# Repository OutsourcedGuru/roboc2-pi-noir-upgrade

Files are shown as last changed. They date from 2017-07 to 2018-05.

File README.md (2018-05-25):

# roboc2-pi-noir-upgrade
Step-by-step instructions for adding a Pi NoIR webcam to the Robo C2 printer.

## Order Parts
For this project, you'll need three mandatory parts and one that's optional. The mandatory parts are the [Raspberry Pi NoIR Camera Board v2 - 8 Megapixels](https://www.adafruit.com/product/3100) ($26.99), a longer [Flex Cable for Raspberry Pi - 18"](https://www.adafruit.com/product/1730) ($2.50) given the distance and lastly, a [medium-sized suction cup](http://www.peakbanner.com/banner-clear-suction-cup-hook-set-4pcs?gclid=CKq-oPKxvtQCFY6cfgodSF4LQQ) ($0.99) from Ace Hardware, for example. I personally purchased my webcam from Fry's Electronics and the ribbon cable from Adafruit.com online.

As for the optional part, I chose to upgrade the microSD on the Robo C2's internal Raspberry Pi 3 from 4GB to 16GB given that the resolution on the new v2 webcam is 8MP (which could be as much as 1GB storage per 8 minutes of video). I chose the [SanDisk Ultra PLUS microSDHC UHS-1 Card with Adapter](http://www.frys.com/product/8654990?site=sr:SEARCH:MAIN_RSLT_PG) from Fry's Electronics ($9.99) for this. The total cost for the full upgrade is about $41 plus tax/shipping, as appropriate, plus any incremental cost to print the enclosure.

Additionally, if your workstation does not have an SD or a microSD slot, you will need some sort of external USB adapter for cloning the microSD card.

## Software
Since we'll be saving an image of the existing microSD and restoring that to the new card, I downloaded and installed [ApplePi-Baker for OS X](https://www.tweaking4all.com/software/macosx-software/macosx-apple-pi-baker/). If you're on Windows for your workstation then you'll need some software to clone microSD cards.

## 3D Part
For this project, you'll need to print the enclosure in PLA. I used the [Robo White PLA](https://store.robo3d.com/collections/filament-pla/products/white-pla-1-kg-spool) for this but any standard PLA filament should work for this.

pi-noir-part

I've created some custom filament profiles for Cura and have stored them in [this repository](https://github.com/OutsourcedGuru/cura-filament-profiles) should you need some. Since it's assumed that you have a Robo C2, I've included the GCODE file which should be ready to print. As a result, you shouldn't even need to go into Cura for this.

## Instructions
Verify that you have all the parts you'll need to begin and a few tools to include a pair of pliers.

required-parts

I purchased two ribbon cables of different lengths (12" and 18") to do some test fitting. If you don't mind the cable being seen inside the black enclosure of the Robo C2 then the 12" will be fine; otherwise, go with the 18" cable as I've done.

It's necessary to do some slight cleanup of the inside of the Pi NoIR printed part but some of the remainder of the support actually is useful to hold the camera in. I didn't find it necessary to use any glue to hold the enclosure together but you'll want to do a test fit later to verify.

### Power on your Robo C2 to raise the bed
Once it has booted, ignore any prompts to upgrade the software at this time by choosing Cancel.

**Motor Control** -> using **Z=100mm** setting, press the **Z-** option once *and only once*! Adjust to the **Z=1mm** setting and continue raising it with **Z-** (but not so high that the bed hits the extruder).

motor-controls

### Save your z-offset
In the LCD menu, select Utilities -> Options -> EEPROM -> Home Offsets and write down your current setting here for Z.

z-offset

It's possible after upgrading your software that this value may be set back to the default. Given that this is a fussy adjustment, it's good to have this information available.

### Power off your Robo C2
Use the power switch in the back to abrubtly power off the printer (without it homing the steppers).

### Remove the base and front covers
Use the latch in the front to remove the base cover. Reach inside to pop loose the front cover at the top. Work around to the latches on the sides and then ease off the front panel. Leave the connections in place.

front-1
front-2
front-3

It's good to have a strong light so that you can see things inside.

### Pull the microSD card
Find the Raspberry Pi 3 computer on the left and locate its microSD card which is just sticking out from the bottom of the board. Slide this out with your fingers.

microsd-location

Using the SD adapter which comes with the new microSD card, insert the existing 4GB microSD card from the Robo C2 into this SD adapter and then into your workstation.

microsd-original

If your workstation does not have an SD adapter slot, you might need a USB adapter which accommodates a microSD card.

### Begin backup of your image
It's probably a good idea to verify that your workstation has at least 4GB of free space. If not, you'll need to clear some up to make this image. In OS X, you right-mouse click the hard drive in Finder and choose Get Info.

available-space

I use ApplePi-Baker for this step. Select the 4GB microSD card from the Robo C2 and choose the Create Backup option. Give your image a useful name and select ZIP as the Format option. Choose Save and while this is backing up, continue with the physical installation of the camera.

backup-1
[backup-2](https://user-images.githubusercontent.com/15971213/27871419-76214bb4-615a-11e7-9f85-c6eaef0330d9.png)

### Replace the ribbon cable on your camera
Unbox the Pi NoIR camera. Push the black clip near the ribbon cable so that it's moved away from the board by a couple of millimeters. Then remove the existing ribbon cable, noting the direction of the silver connectors at the end.

ribbon-1
ribbon-2

Insert one end of the new 18" replacement ribbon cable, making sure that the silver connectors face the same way as before. Push the black clip back down into place so that it will hold the ribbon cable snugly.

ribbon-3
ribbon-4
ribbon-5

Remove the small protective film from the camera's lens and discard.

ribbon-6

### Assemble the enclosure
Insert the Pi NoIR camera into the base of the newly-printed enclosure. Verify that it sits evenly and that the ribbon goes through the available slot.

Align the top of the enclosure so that the hole is aligned properly with the lens. Snap the two together. If necessary, cover everything with something to protect from scratches and use some pliars to gently push both together.

Remove any hooks from the suction cup and insert it into the slot in the rear.

enclosure

### Complete backup image
The backup of the microSD should be finished at some point. Remember to eject the microSD properly before removing it from your workstation.

backup-3

Exit completely from the ApplePi-Baker software.

### Begin restoring to the new microSD card
Insert the new 16GB microSD into the SD adapter and put it into your workstation. Start the ApplePi-Baker software again and select the microSD card.

restoral-1

In the restore section, find the image file you created earlier and restore to this new 16GB microSD card. Choose Restore and go back to the physical installation of the camera while this is taking place.

restoral-2

### Install the ribbon cable
Place the Pi NoIR and enclosure on the inside left blue panel and orient it so that it faces the bed. Route the ribbon cable through the side slot and angle it toward the front bottom of the printer. Continue pushing/pulling the ribbon cable until you see its end. Grab the ribbon cable from here and route it around the corner and to where the top of the Raspberry Pi 3 computer is located.

cabling-1

As you did before, gently pull up the black clip from the ribbon cable connection in the center area of the Raspberry Pi computer. Connect the ribbon cable so that its silver connectors face you and push down the black clip completely.

cabling-2
cabling-3
cabling-4

Use a bright light to verify that you've correctly connected the ribbon cable and that the black clip is down on both sides.

cabling-5

Take up the ribbon cable's slack in the opposite direction, straighten the ribbon cable above the slit on the left side of the printer and afix the suction cup so that it's high enough to see the bed in its highest position. Viewing it from the outside, rotate the camera so that its top is horizontal.

cabling-6
cabling-7

Viewing the Pi NoIR from the front of the printer, verify that its front will not interfere with the left-most position of the extruder head assembly. It shouldn't, given the current design.

### Complete restoral
The restoral for the microSD image should be completed at some point. ApplePi-Baker is usually good enough to eject the volume when finished but verify this, eject when everything is done before physically removing the adapter.

### Reinstall the new microSD card
Carefully install the new 16GB microSD card into the Raspberry Pi 3 inside the Robo C2 printer. The connectors should be facing up.

I found that gently grasping the card diagonally with a pair of pliers was the only way to position the card into the slot. I then used a finger to push it all the way into place.

### Replace front and base covers
Reinstall the front cover beginning with the bottom and working up the sides and top latches. Reinstall the base cover.

### Power on Robo C2
Turn on the power switch for the printer and wait for it to boot. Ignore any upgrade prompts by choosing Cancel.

Under Motor Controls, choose the Home feature to return all steppers to their home position.

### Make some adjustments remotely and test the camera
Using ssh (OS X) or putty (Windows) from your workstation, connect to your printer using its name (serial number from the label on the back).

Note that my printer's name is **charming-pascal** but yours should be something different. The default password should be **raspberry**.

```
$ ssh pi@charming-pascal.local
$ sudo raspi-config
  # choose Expand Filesystem
  # choose Enable Camera
  # when prompted to reboot, choose No
  # choose Finish
$ cd ~
$ mkdir photos
$ cd photos
$ raspistill -o first-light.jpg
$ ls
first-light.jpg
$ sudo reboot
```

After the raspistill command, you should see the captured image for a moment on the Robo's LCD screen.

### Turn on the camera in OctoPrint
The Robo should reboot after that last command. Back in your workstation, bring up a browser and visit the OctoPrint interface, replacing the printer's name below with your own.

```
$ open http://charming-pascal.local
```

In Settings -> Plugins -> Robo, check the Enable Webcam checkbox and choose Save.

Under the System menu, choose Start video stream.

video-1

In Settings -> Webcams & Timelapse, choose the Test option. You should see an image from the webcam.

video-2

### Update the software
In Settings -> Software Update, choose Check for update now.

On the LCD screen of the Robo, choose Utilities, Update.

### Verify timelapse and video streaming
After any reboots, go back into OctoPrint. Turn on the video streaming again from the System menu option. Refresh/reload the page.

Send a job to be printed, noting the video streaming panel lower on the home page itself.

video-3

Lower on the home page, adjust any settings under Time Lapse.

video-4

...versus...

video-5

After the print job has completed, review the time-lapse video which has been created. An example video is here in this repository if you'd like to see how my botched print job finished badly one third of the way through--I quickly aborted the job, btw.

You may want to adjust the location of the suction cup a little higher/lower depending upon your first results as well as slightly rotating it (if your Pi NoIR's camera wasn't perfectly aligned during its manufacture).

### Remove the OctoPrint watermark in your videos
There's also a bit of a hack so that you can remove the OctoPrint watermark there in the bottom/left of the videos it produces.

```
$ ssh pi@charming-pascal.local
$ cd ~/.octoprint
$ sudo nano config.yaml
  # locate the webcam: section near the bottom of the file and between ffmpeg: and snapshot: lines insert the line...
  watermark: false
  # save the file with Ctrl+O, Enter then Ctrl+X
$ exit
```

Next, you'll want to go into OctoPrint from your workstation and restart the service from the System menu.

### Adjust the rotation in OctoPrint
Unfortunately, it looks like the camera included in the Robo R2 has a default tilt of 10° for whatever reason. The streaming side of the webcam doesn't adjst this, so time-lapse videos turn out fine. It is annoying, though, to see this unwanted rotation in the interface. Here's how to remove that, noting that you may have to repeat this with every upgrade from Robo.

Substitute your own printer's name below.

```
$ ssh pi@charming-pascal.local
$ sudo nano ~/oprint/lib/python2.7/site-packages/octoprint_robotheme/static/css/main.css
  # ---------------------------
  # Use the Ctl-W command to search for "rotate"
  # (pressing Enter)...
  # then comment out the three offending lines
  # using the style of commenting that I'm using here
  # ---------------------------
    #webcam_image {
      position: relative;
      top: -54px;
      left: -47px;
      /*-ms-transform: rotate(-10deg);*/
      /*-webkit-transform: rotate(-10deg);*/
      /*transform: rotate(-10deg);*/
    } 
  # ---------------------------
  # save the file with Ctrl+O, Enter then Ctrl+X
  # ---------------------------
$ exit
```

It may be necessary to restart the OctoPrint interface for this change to be seen.

|Donate||Cryptocurrency|
|:-----:|---|:---:|
| eth-receive || btc-receive |
|Ethereum||Bitcoin|

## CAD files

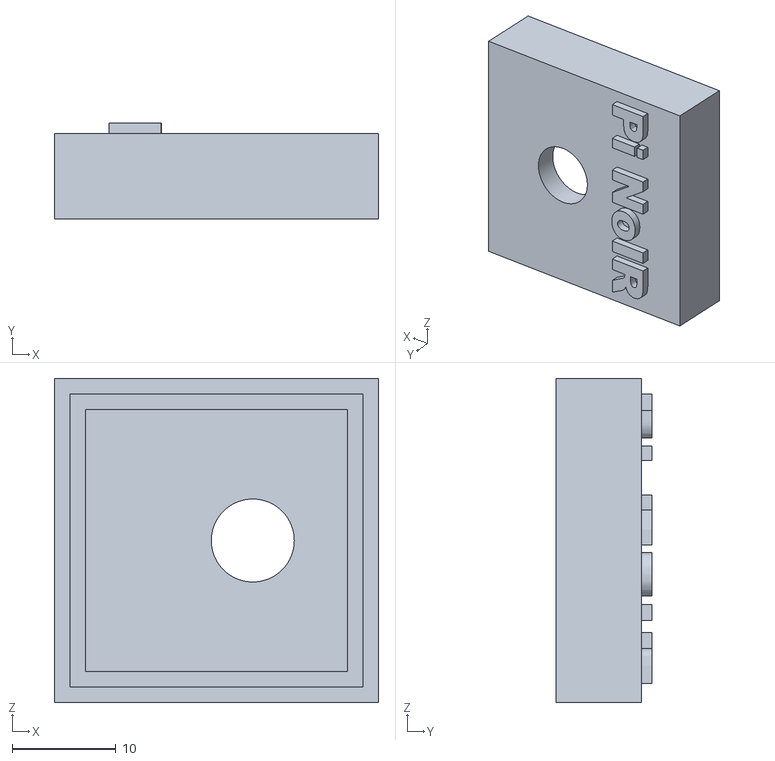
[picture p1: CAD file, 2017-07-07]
Pi-NoIR-Front.stl
31.2 x 9.25 x 31.2

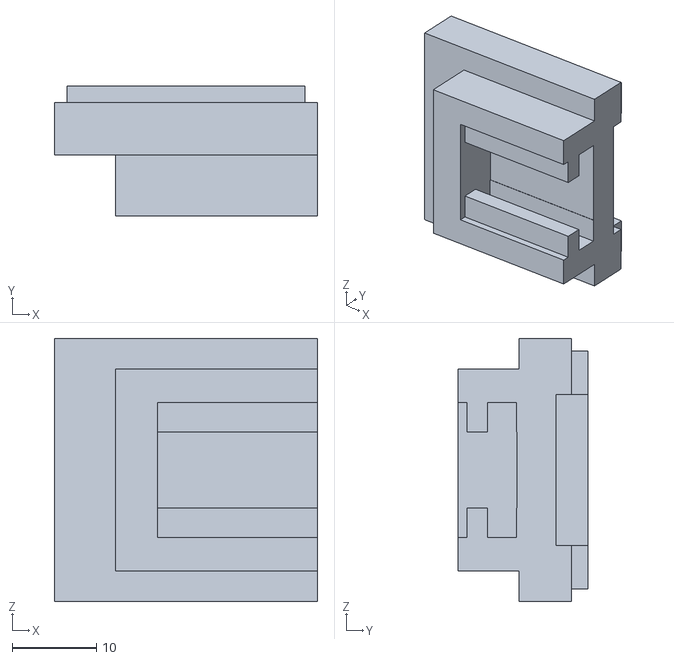
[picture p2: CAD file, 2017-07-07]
Pi-NoIR-Back.stl
31.2 x 15.5 x 31.2

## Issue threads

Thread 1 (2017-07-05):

Placeholder for README.md images

OutsourcedGuru, 2017-07-05:
Enclosure
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

OutsourcedGuru, 2017-07-05:
Required Parts
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

OutsourcedGuru, 2017-07-05:
Z-Offset setting
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

OutsourcedGuru, 2017-07-05:
Motor Controls
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

OutsourcedGuru, 2017-07-05:
Removing the front cover
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

OutsourcedGuru, 2017-07-05:
microSD location
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

OutsourcedGuru, 2017-07-05:
microSD original
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

OutsourcedGuru, 2017-07-05:
Available space
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

OutsourcedGuru, 2017-07-05:
Backing up and then ejecting the original microSD
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

OutsourcedGuru, 2017-07-05:
Replacing with the longer 18" ribbon cable
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

OutsourcedGuru, 2017-07-05:
Assembled enclosure
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

OutsourcedGuru, 2017-07-05:
Restoral
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

OutsourcedGuru, 2017-07-05:
Cabling
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

OutsourcedGuru, 2017-07-05:
Videos
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

Closed 2018-01-20.
